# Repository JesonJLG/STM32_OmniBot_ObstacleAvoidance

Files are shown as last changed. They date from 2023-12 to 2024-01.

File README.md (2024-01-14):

## 课设题目

基于stm32的麦轮避障小车设计

## 主要任务

利用stm32f103最小系统板+相关硬件模块的方式搭建硬件平台，基于stm32库函数进行c语言编程，最终实现避障小车的实地运行。

## 详细功能描述

### 核心功能：

1. 手机app蓝牙遥控功能实现

2. 基于麦克纳姆轮的全向运动系统设计与实现

3. 在小车麦轮遥控功能的基础上迭代，增加**摇头避障、手机重力感应遥控**功能

### 其他功能：

1. 蜂鸣反馈功能
2. 速度检测与显示（测速）
3. 温度检测与显示（测温）

### 项目成果：

手机APP遥控界面展示：

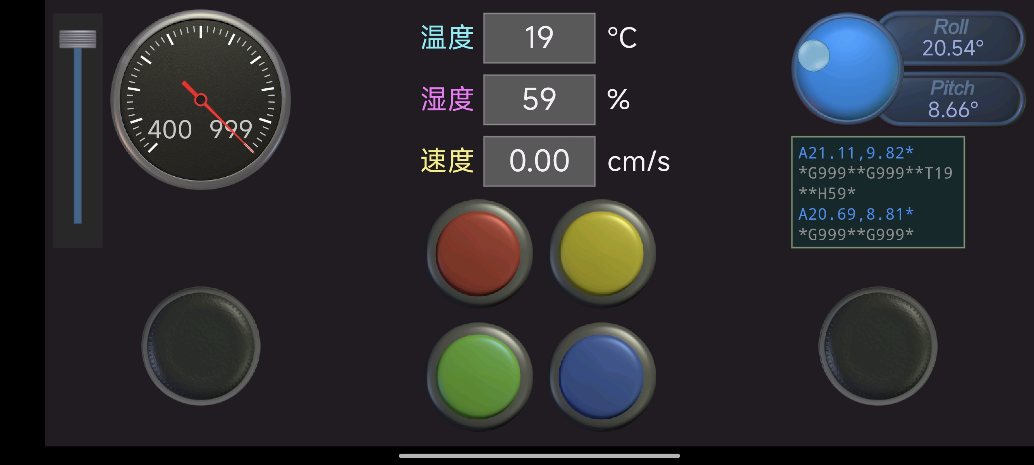
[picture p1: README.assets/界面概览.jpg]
界面概览


实物展示：

（后期测试中因误操作不慎将stm32f103c8t6最小系统板烧了，这里换用正点原子的stm32f103zet6精英板作为候补，各模块引脚均采用宏定义，故简单改动宏定义引脚即可成功移植到精英板，接线会比较麻烦）

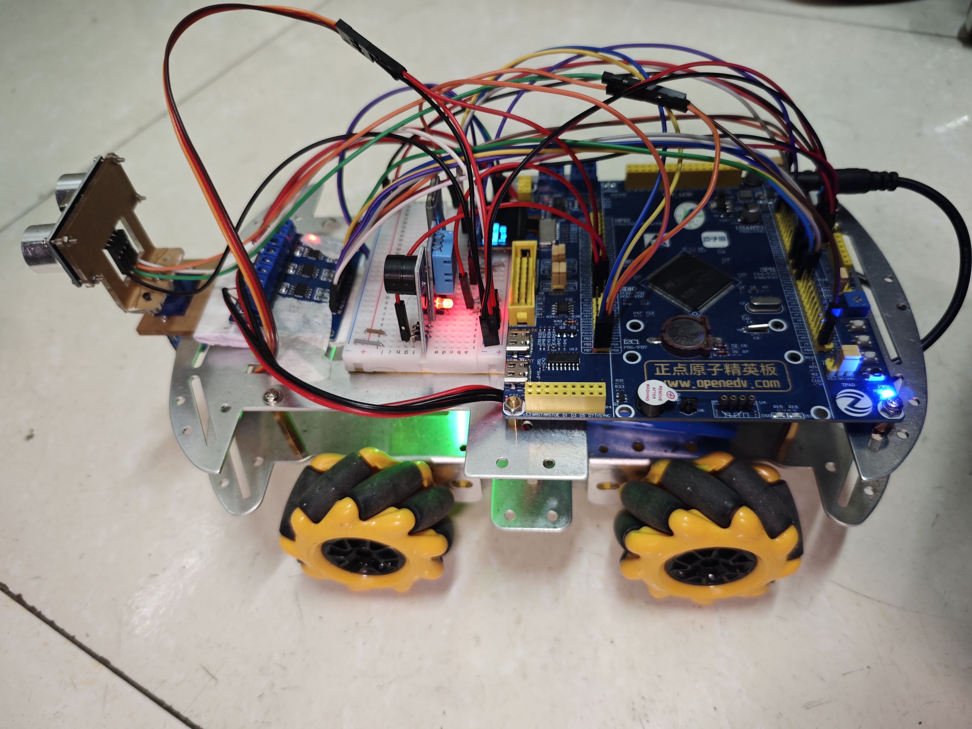
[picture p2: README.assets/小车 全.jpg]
小车 全


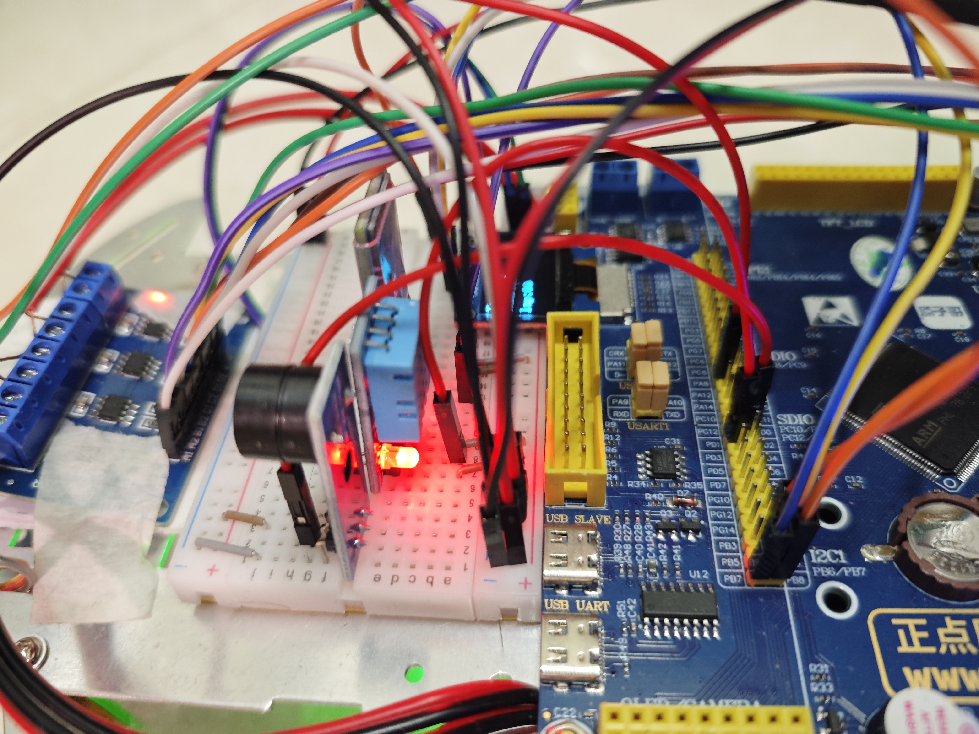
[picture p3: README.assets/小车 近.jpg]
小车 近


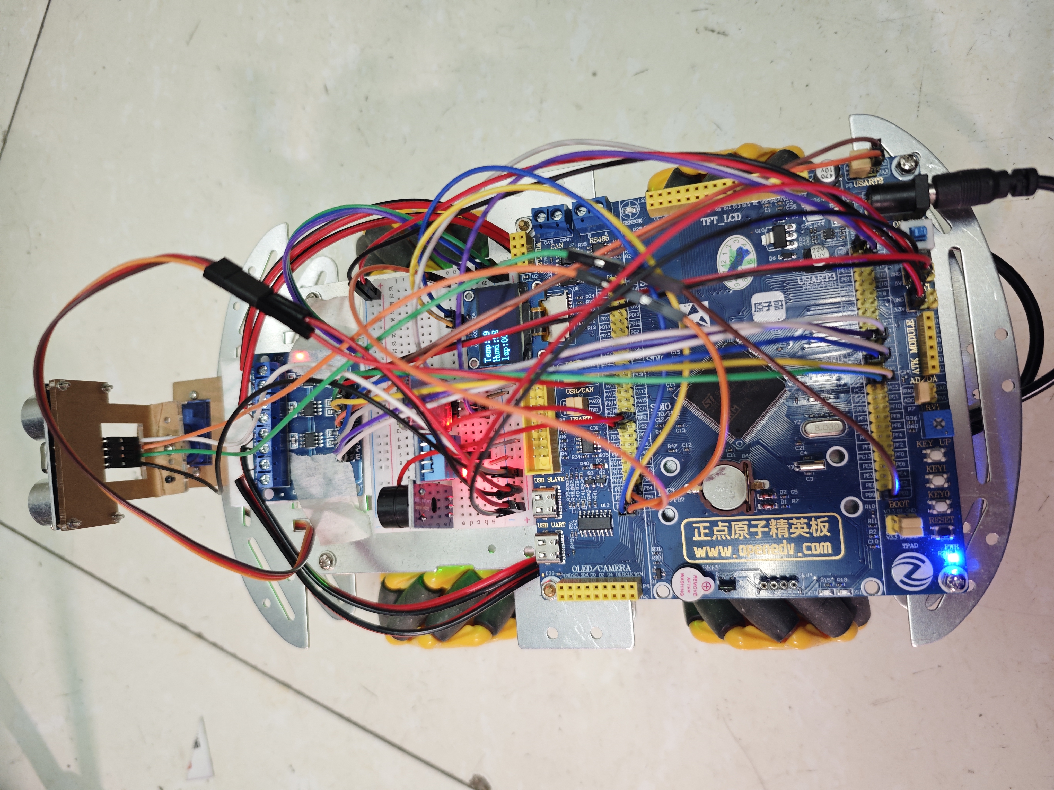
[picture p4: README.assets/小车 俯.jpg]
小车 俯


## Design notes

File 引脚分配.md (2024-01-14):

### 引脚分配

**printf串口**	USART1	PA9(TX)、PA10(RX)

**蓝牙串口**

```c
#define USART_PORT	GPIOB
#define USART_TX	GPIO_Pin_10	//PB10
#define USART_RX	GPIO_Pin_11	//PB11
#define USARTX		USART3
```

**LED指示灯**

```c
#define LED0_PORT	GPIOC
#define LED0_PIN	GPIO_Pin_13
```

```c
/*正点原子精英板*/
#define LED0_PORT	GPIOB		//DS0
#define LED0_PIN	GPIO_Pin_5	
#define LED1_PORT	GPIOE		//DS1
#define LED1_PIN	GPIO_Pin_5	
```

**四个电机**

```c
/*------------添加引脚宏定义-------------*/
/*
左后MotorA(A1,A2): PB1,PB0	TIM3_43
左前MotorB(B1,B2): PA7,PA6	TIM3_21
右前MotorC(C1,C2): PA3,PA2	TIM2_43
右后MotorD(D1,D2): PA1,PA0	TIM2_21
*/
#define MOTOR_PORT_A		GPIOB
#define MOTOR_PORT_BCD		GPIOA

#define MOTOR_TIM_AB		TIM3
#define MOTOR_TIM_CD		TIM2
///左后电机
#define MOTORA_A1		GPIO_Pin_1		//PB1
#define MOTORA_A2		GPIO_Pin_0		//PB0
///左前电机
#define MOTORB_B1		GPIO_Pin_7		//PA7
#define MOTORB_B2		GPIO_Pin_6		//PA6
///右前电机
#define MOTORC_C1		GPIO_Pin_3		//PA3
#define MOTORC_C2		GPIO_Pin_2		//PA2
///右后电机
#define MOTORD_D1		GPIO_Pin_1		//PA1
#define MOTORD_D2		GPIO_Pin_0		//PA0
```

**超声波传感器**

```c
//超声波硬件接口定义
#define HCSR04_PORT     GPIOB
#define HCSR04_CLK      RCC_APB2Periph_GPIOB
#define HCSR04_TRIG     GPIO_Pin_8
#define HCSR04_ECHO     GPIO_Pin_9
```

**舵机**

```c
#define SERVO_PORT	GPIOA
#define SERVO_PWM	GPIO_Pin_8
#define SERVO_TIM	TIM1
```

**OLED**

```c
#define OLED_PORT	GPIOB
#define OLED_SCL	GPIO_Pin_6
#define OLED_SDA	GPIO_Pin_7
```

**蜂鸣器**

```c
#define BEEP_PORT	GPIOC
#define BEEP_DIO	GPIO_Pin_14
```

```c
/*正点原子精英板*/
#define BEEP_PORT	GPIOD
#define BEEP_DIO	GPIO_Pin_0
```

**温度传感器**

```c
#define DHT11_PORT	GPIOC
#define DHT11_DATA	GPIO_Pin_15
```

```c
/*正点原子精英板*/
#define DHT11_PORT	GPIOD
#define DHT11_DATA	GPIO_Pin_1
```

**对射红外传感器**

```c
#define CNTSSR_PORT	GPIOB
#define CNTSSR_DO	GPIO_Pin_4
#define CNTSSR_EXTI	EXTI_Line4
```

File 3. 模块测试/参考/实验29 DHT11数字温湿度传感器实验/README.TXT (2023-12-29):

实验器材:
	正点原子精英STM32F103开发板
实验目的:
	学习DHT11数字温湿度传感器的使用.
	
硬件资源:
	1,DS0(连接在PB5)
	2,串口1(波特率:115200,PA9/PA10连接在板载USB转串口芯片CH340上面)
	3,ALIENTEK 2.8/3.5/4.3/7寸TFTLCD模块(通过FSMC驱动,FSMC_NE4接LCD片选/A10接RS) 
	4,DHT11传感器一个(接在PG11上). 
	
实验现象:
	本实验开机的时候先检测是否有DHT11存在，如果没有，则提示错误。只有在检测到DHT11之后才开始读取温湿
	度值，并显示在LCD上，如果发现了DHT11，则程序每隔100ms左右读取一次数据，并把温湿度显示在LCD上。同
	样我们也是用DS0来指示程序正在运行。
	 
注意事项:
	1,4.3寸和7寸屏需要比较大电流,USB供电可能不足,请用外部电源适配器(推荐外接12V 1A电源).
	2,本例程在LCD_Init函数里面(在ILI93xx.c),用到了printf,如果不初始化串口1,将导致液晶无法显示!!
	3,需自备DHT11数字温湿度传感器一个，并插在开发板的U4位置（根据丝印插，网面朝外） 

-------------------------------------------------------------------------------------------
◆其他重要连接：
  开发板光盘资料下载地址（视频+文档+源码等）：http://www.openedv.com/posts/list/13912.htm
  添加微信公众平台方法：http://www.openedv.com/posts/list/45157.htm

◆友情提示：如果您想以后及时免费的收到正点原子所有开发板资料更新增加通知，请关注微信公众平台：

 2种添加方法：（动动手提升您的学习效率，惊喜不断哦）
（1）打开微信->添加朋友->公众号->输入“正点原子”->点击关注
（2）打开微信->添加朋友->输入“alientek_stm32"->点击关注

 具体微信添加方法，请参考帖子：http://www.openedv.com/posts/list/45157.htm

			正点原子@ALIENTEK 
			广州市星翼电子科技有限公司
			电话：020-38271790
			传真：020-36773971
			购买：http://eboard.taobao.com
			公司网站：www.alientek.com
			技术论坛：www.openedv.com

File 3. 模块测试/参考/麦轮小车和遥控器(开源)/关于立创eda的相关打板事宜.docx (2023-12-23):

《关于立创eda的相关打板事宜》（个人经验，求生欲极强）

首先，成为立创eda的注册用户之后，每个月会可以在下单助手的初始界面的右下角

免费券领取（图一）中获得两张1-4层板，和一张6层板的选择权（图二），具体选择由个人自己决定（打几层的板子就用相应的优惠券）。

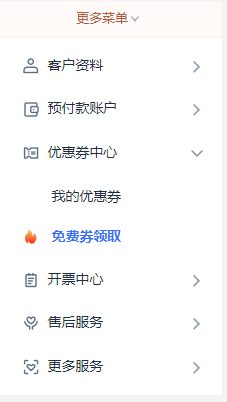
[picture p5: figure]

图一

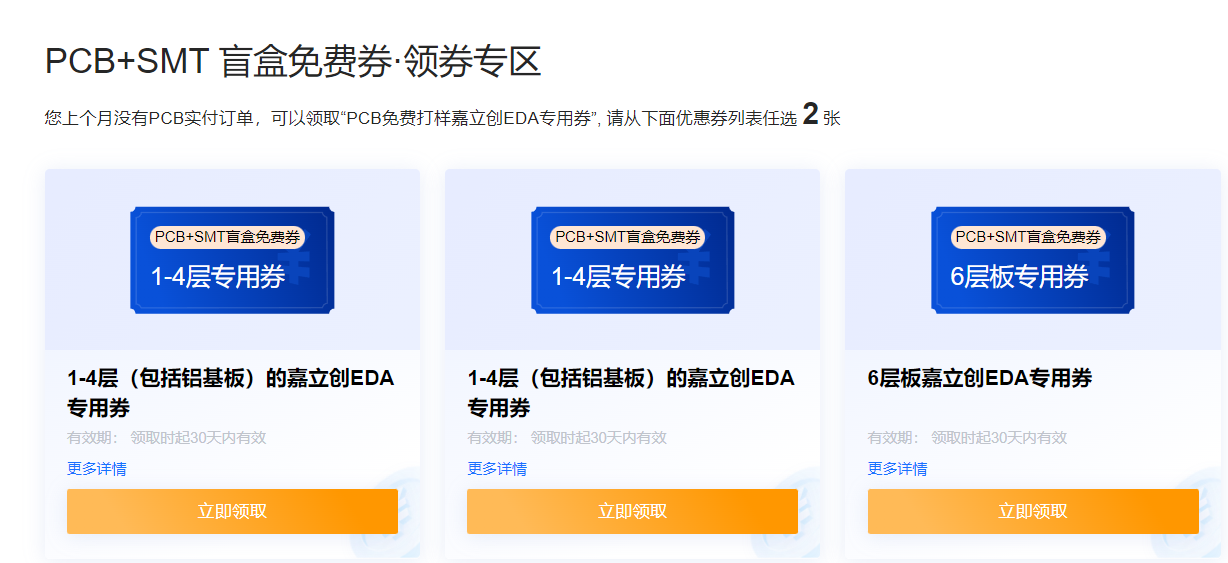
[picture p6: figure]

图二

之后就可以在pcb下单界面上传文件进行下单（注意，上传文件需要以压缩包形式上传，up主的是已经搞好的Gerber文件，所以直接上传就好，如果有自己绘制的pcb但是不是使用eda，比如使用AD的，生成的文件需要自己压缩上传，但是现在AD上传的pcb没法使用优惠券，所以建议想要节省成本的同志们使用立创eda）。

上传文件后板子的基础信息（图三）是自动出现的，层数和尺寸都是自动检测的（目前嘉立创允许的最大免费打印尺寸是10cm x 10cm），唯一需要自己决定的是板子数量，想要免费打板的话数量只能选择为5。

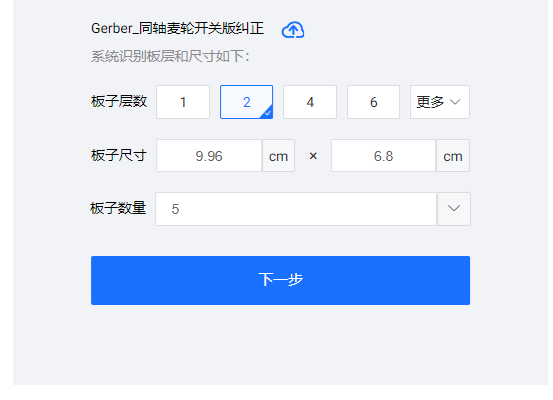
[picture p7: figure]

图三

板材类型选择FR-4即可（其他的可能不免费）。基本信息（图四）在选完板材类型后其他的保持不变即可。

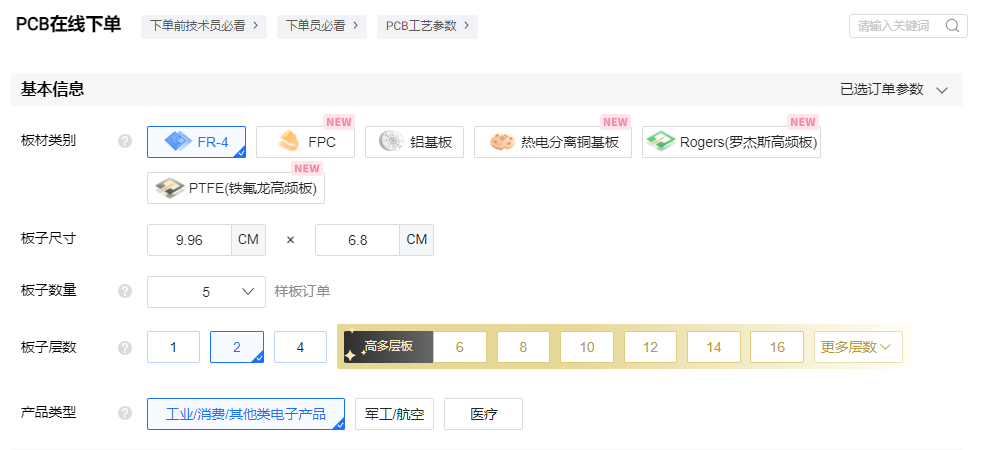
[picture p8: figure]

图四

重要事项（图五），确认生产稿就选不需要（除非想花钱）。

图五

Pcb工艺信息中拼版款数视上传文件而定，一般为1块；板子厚度为1.6；板材选项为无要求（不加价才是王道）；外层铜厚为1盎司；阻焊颜色自己选择即可（本人推荐黑色，又酷，焊出来之后看着也不是很脏，搭配洗板水清洁后效果更佳，但是需要注意的是除了绿色的板子一般48小时可以完工之外，其他所有的颜色都需要三天左右，如果急用的话建议默认绿色）；字符颜色系统默认不去管他；阻焊覆盖使用默认的过孔盖油即可（其他的要么不给用，要么得加钱）；焊盘焊盘喷镀就选有铅喷锡（问就是其他的要加钱）；不选沉金，沉金厚度就不用管；下面两项默认就好。总体如下图六

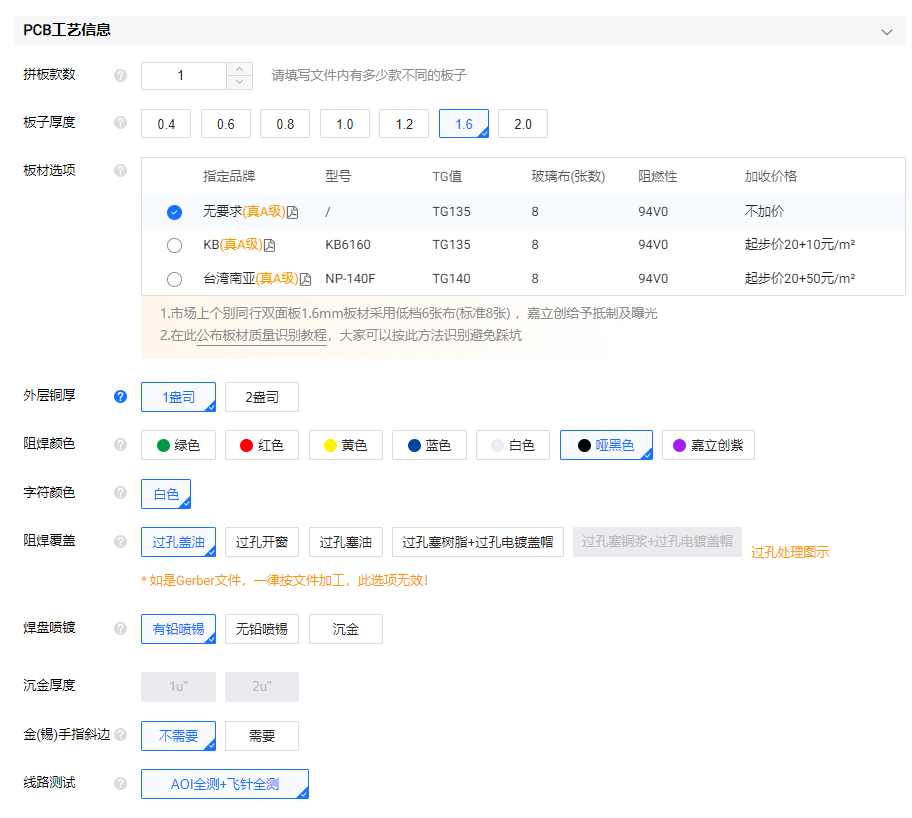
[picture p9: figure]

图六

选择交期，看个人的需求（图七）。

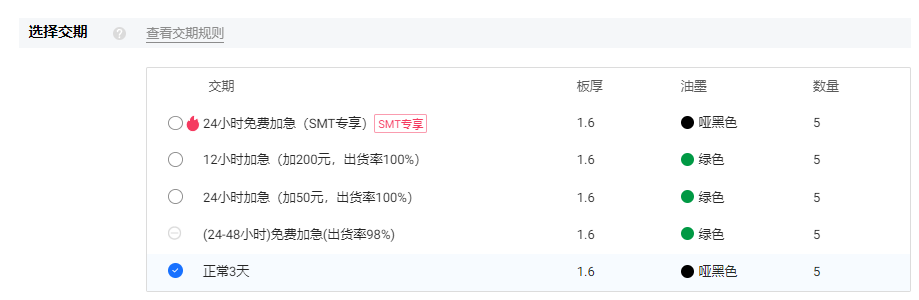
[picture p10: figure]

图七

个性化服务默认就好（图八）。

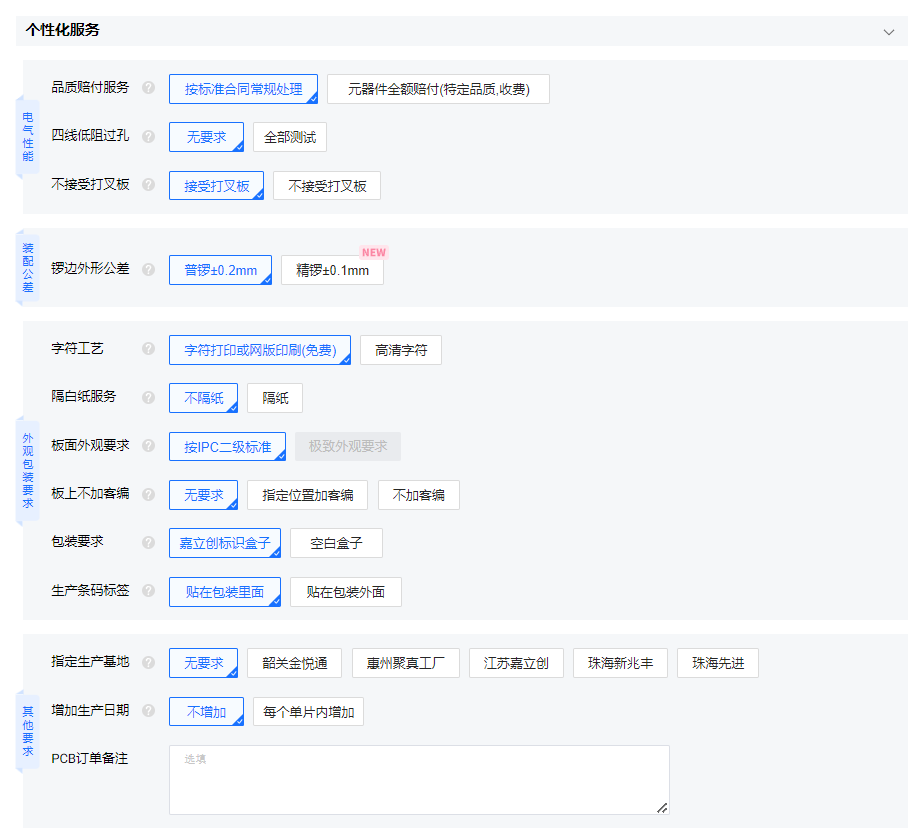
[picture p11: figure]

图八

关于SMT贴片（图九），如果对自己的焊接水平不够自信，选择此选项，eda会根据板子所需的的元器件封装在立创商城中选择对应的元器件帮你焊上（由于得加钱，本人从来没用过此选项，不知道是不是这样，不对勿喷）。

图九

关于激光钢网选项（图十），是根据pcb所用的贴片封装开相对应的钢网，目的是挤锡膏（一般使用无铅低温锡膏，一般为针管式，挤在需要放置元器件的位置上，购买加热台，将pcb放置在加热台上，待一段时间后锡膏加热为普通闪闪发亮的锡时，视情况用镊子将加热时移动的元器件调回原位。）的时候方便快捷（由于得加钱，本人从来没用过此选项，不知道是不是这样，不对勿喷）。

图十

关于完善开票信息（图十一），个人的话选择个人/普通电子发票即可，并且第一次使用时需要完善开票资料；关于地址和联系方式，各位同志想必都非常清楚。

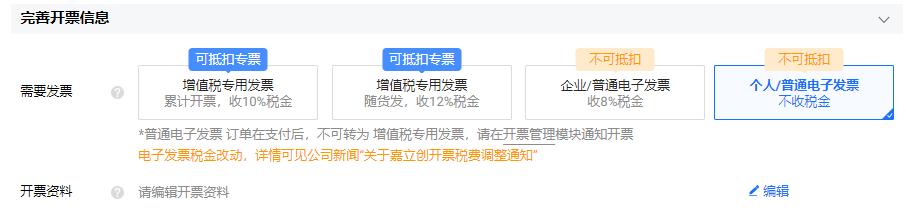
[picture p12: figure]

图十一

发货信息（图十二），收据/送货单使用电子收据单（省钱）；发货方式视情况自己决定。

图十二

选择快递（图十三），视个人情况而定。

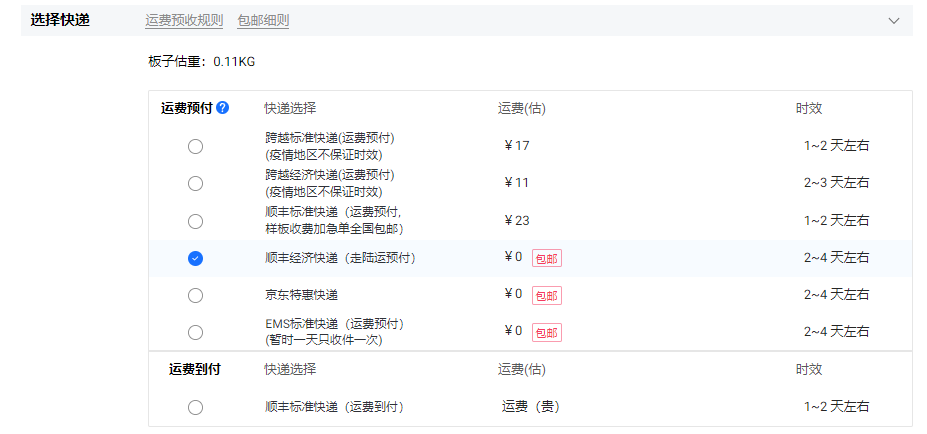
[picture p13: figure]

图十三

其他信息（图十四），个人建议手动确认，如果没有使用优惠券，不能白嫖岂不是肠子都悔青了？

图十四

最后就可以提交订单了，订单提交后，如果是手动付款的话，客服会对文件进行审核，审核通过后在图十五所示选项中查看订单信息，进行相应的付款手续（按照我上面的操作一般都是免费的）。最终效果图如图十六（本人以前打的pcb板，属于已经接收的完成状态，具体状态视情况为正在生产等）所示。

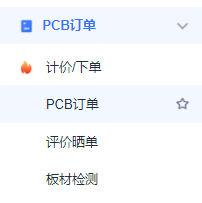
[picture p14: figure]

图十五

图十六

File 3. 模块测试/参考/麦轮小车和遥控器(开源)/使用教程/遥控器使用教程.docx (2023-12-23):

1、 左边摇杆往左或往右拨进行模式切换
2、 右边摇杆右拨进入当前模式
3、 右边摇杆左拨退出当前模式(除遥控模式外)
4、 遥控器前倾大于50度，退出遥控模式，因为遥控模式需要摇杆控 制小车运动，所以通过体感退出当前模式
5、 贪吃蛇模式蛇的运动方向由左摇杆控制
6、 遥控器的蓝牙只用于开发程序时起调试作用

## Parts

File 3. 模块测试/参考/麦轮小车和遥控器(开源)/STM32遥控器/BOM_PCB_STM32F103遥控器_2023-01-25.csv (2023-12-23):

ID | Name | Designator | Footprint | Quantity | Manufacturer Part | Manufacturer | Supplier | Supplier Part | Price
1 | 104 | C9,C6 | C0805 | 2
2 | 10k | R3,R6,JR1,JR2,R1,R2 | R0805 | 6
3 | OLED | H1 | OLED | 1
4 | 10uF | AC1 | C0805 | 1
5 | 22uF | AC2 | C0805 | 1
6 | 105 | C1,C2,C3,C4,C5 | C0805 | 5
7 | 22P | C7,C8 | C0805 | 2
8 | 100nF | JC1,JC2,JC3,JC4,JC5,JC6 | C0805 | 6
9 | AMS1117-3.3 | AU1 | SOT-223-3_L6.5-W3.4-P2.30-LS7.0-BR | 1 | AMS1117-3.3 | PUOLOP | LCSC | C351784 | 0.4095
10 | JDY-23蓝牙模块 | H2 | JDY-23蓝牙模块 | 1
11 | MPU6050模块 | H3 | MPU6050模块 | 1
12 | NRF24L01无线模块 | H4 | NRF24L01无线模块 | 1
13 | 2.54-1*4P反弯排针 | H9 | HDR-TH_4P-P2.54-H-M-W10.4 | 1 | 2.54-1*4P反弯排针 | BOOMELE(博穆精密) | LCSC | C91552 | 0.1356
14 | 510R | R4,R5 | R0805 | 2
15 | 1M | R9 | R0805 | 1
16 | JoyStick | JU1,JU2 | JOYSTICK | 2
17 | K2-3.6×6.1_SMD | KEY1 | KEY-SMD_2P-L6.2-W3.6-LS8.0 | 1 | K2-1107ST-A4SW-06 |  | LCSC | C118141 | 0.4331
18 | LED-0805_R | LED1 | LED0805_RED | 1 | 17-21SURC/S530-A3/TR8 | EVERLIGHT(台湾亿光) |  | C72037 | 0.1145
19 | LED-0805_G | LED2 | LED0805_GREEN | 1 | NCD0805G1 | 国星光电 |  | C84260 | 0.1261
20 | CONN-TH_2P-P5.00 | P2 | CONN-TH_2P-P5.00 | 1 |  |  | LCSC
21 | SS-12D06L5 | SW3 | SS-12D06 | 1 | SS-12D06L5 | XKB Enterprise | LCSC | C319015 | 2.1989
22 | STM32F103C8T6 | U1 | STM32F103C8T6LQFP-48_L7.0-W7.0-P0.50-LS9.0-BL | 1 |  |  | LCSC
23 | 8M | X1 | HC-49US_L11.5-W4.5-P4.88 | 1 | XIHCELNANF-8MHZ | TAITIEN Elec | LCSC | C295088 | 0.7692

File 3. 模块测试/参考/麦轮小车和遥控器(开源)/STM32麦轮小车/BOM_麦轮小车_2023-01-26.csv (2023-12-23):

ID | Name | Designator | Footprint | Quantity | Manufacturer Part | Manufacturer | Supplier | Supplier Part | Price
1 | 10uF | AC1 | C0805 | 1
2 | 22uF | AC2 | C0805 | 1
3 | AMS1117 | AU1 | AMS1117-3.3 | 1
4 | 105 | C1,C2,C3,C4,C5 | C0805 | 5
5 | 104 | C6 | C0805 | 1
6 | 22P | C7,C8 | C0805 | 2
7 | 100nF | C9,C10,C11,C12,C13,C14 | C0805 | 6
8 | HX25035-2A | CN1,CN2,CN3,CN4 | CONN-TH_P2.50_HX25035-2A | 4 | HX25035-2A | HX(红星) | LCSC | C442378 | 0.0935
9 | HDR-F-2.54_1x8 | H1,H3,H5,H6 | HDR-F-2.54_1X8 | 4 |  |  | LCSC | C225505 | 1.1165
10 | JDY-23蓝牙模块 | H2 | JDY-23蓝牙模块 | 1
11 | NRF24L01无线模块 | H4 | NRF24L01无线模块 | 1
12 | HDR-F-2.54_1x4 | H15 | HDR-F-2.54_1X4 | 1 |  |  | LCSC | C225501 | 0.4928
13 | STlink | H16 | STLINK | 1
14 | K2-3.6×6.1_SMD | KEY1 | KEY-SMD_2P-L6.2-W3.6-LS8.0 | 1 | K2-1107ST-A4SW-06 |  | LCSC | C118141 | 0.4331
15 | LED-0805_R | LED9 | LED0805_RED | 1 | 17-21SURC/S530-A3/TR8 | EVERLIGHT(台湾亿光) |  | C72037 | 0.1145
16 | LED-0805_G | LED10 | LED0805_GREEN | 1 | NCD0805G1 | 国星光电 |  | C84260 | 0.1261
17 | WS2812B-V5/W | LED11,LED12,LED13,LED14,LED15,LED16 | LED-SMD_L5.0-W5.0-P3.20-LS5.4-TL | 6 | WS2812B-V5/W | worldsemi | LCSC | C2874885 | 0.6626
18 | CONN-TH_2P-P5.00 | P2 | CONN-TH_2P-P5.00 | 1 |  |  | LCSC
19 | 10k | R1,R2 | R0805 | 2
20 | 510R | R4,R5 | R0805 | 2
21 | 1M | R9 | R0805 | 1
22 | SS-12D06L5 | SW3 | SS-12D06 | 1 | SS-12D06L5 | XKB Enterprise | LCSC | C319015 | 2.1989
23 | STM32F103C8T6 | U1 | STM32F103C8T6LQFP-48_L7.0-W7.0-P0.50-LS9.0-BL | 1 |  |  | LCSC
24 | Mini降压模块 | U2 | MINI降压模块 | 1
25 | 8M | X1 | HC-49US_L11.5-W4.5-P4.88 | 1 | XIHCELNANF-8MHZ | TAITIEN Elec | LCSC | C295088 | 0.7692

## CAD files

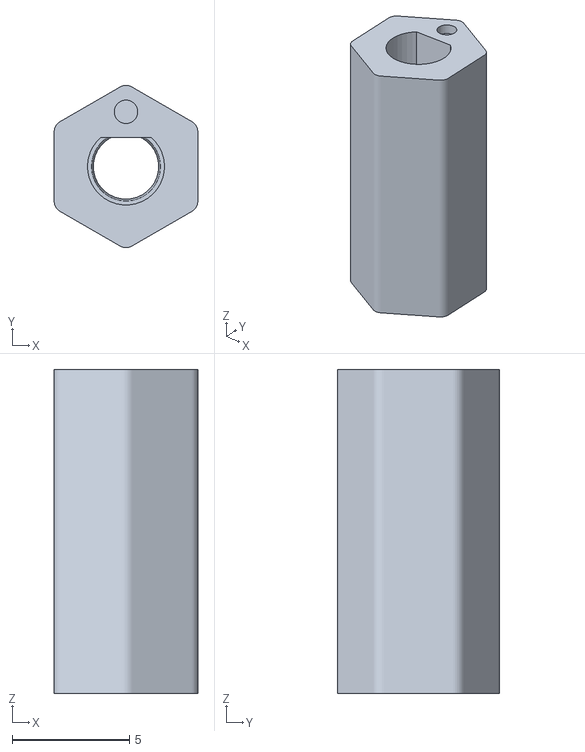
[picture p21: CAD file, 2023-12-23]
3. 模块测试/参考/麦轮小车和遥控器(开源)/3D打印模型/N20电机配件3D文件/48mm麦轮联轴器(打印误差难控制).STL
6.12 x 6.91 x 13.8

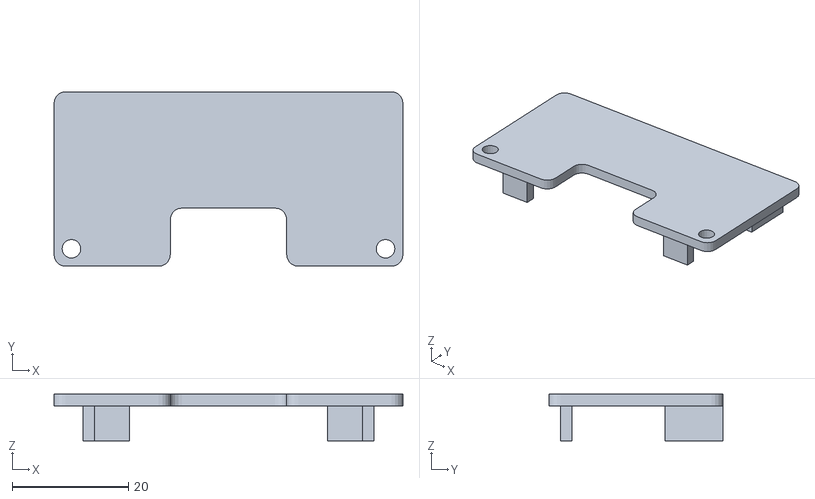
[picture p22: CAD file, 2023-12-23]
3. 模块测试/参考/麦轮小车和遥控器(开源)/3D打印模型/麦轮小车电池支架.stl
60.0 x 30.0 x 8.00

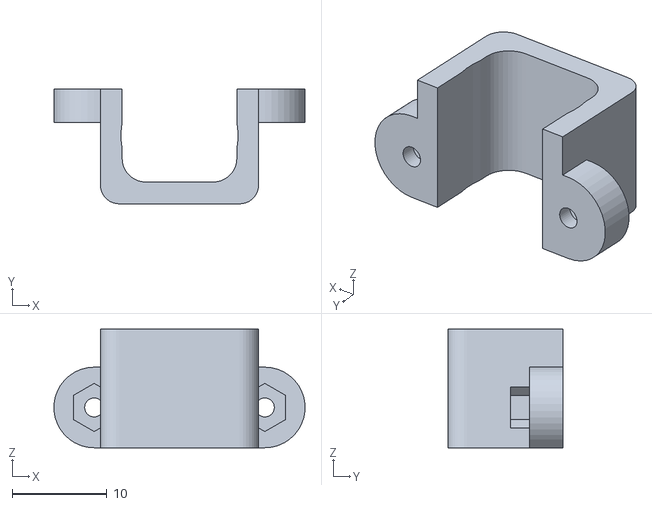
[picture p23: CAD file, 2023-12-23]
3. 模块测试/参考/麦轮小车和遥控器(开源)/3D打印模型/N20电机配件3D文件/N20电机固定座.STL
26.5 x 12.1 x 12.5

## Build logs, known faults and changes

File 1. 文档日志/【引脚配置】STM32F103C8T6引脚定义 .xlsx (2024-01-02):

STM32F103C8T6引脚定义表
引脚号 | 引脚名称 | 类型 | I/O口电平 | 主功能 | 默认复用功能 | 重定义功能
1 | VBAT | S |  | VBAT
2 | PC13-TAMPER-RTC | I/O |  | PC13 | TAMPER-RTC |  | 特殊功能待定 |  | LED
3 | PC14-OSC32_IN | I/O |  | PC14 | OSC32_IN |  |  |  | BEEP
4 | PC15-OSC32_OUT | I/O |  | PC15 | OSC32_OUT |  |  |  | DHT11
5 | OSC_IN | I |  | OSC_IN
6 | OSC_OUT | O |  | OSC_OUT
7 | NRST | I/O |  | NRST
8 | VSSA | S |  | VSSA
9 | VDDA | S |  | VDDA
10 | PA0-WKUP | I/O |  | PA0 | WKUP/USART2_CTS/ADC12_IN0/TIM2_CH1_ETR |  | USART2/ADC12_0123/TIM2_1234 |  | 右后电机D
11 | PA1 | I/O |  | PA1 | USART2_RTS/ADC12_IN1/TIM2_CH2
12 | PA2 | I/O |  | PA2 | USART2_TX/ADC12_IN2/TIM2_CH3 |  |  |  | 右前电机C
13 | PA3 | I/O |  | PA3 | USART2_RX/ADC12_IN3/TIM2_CH4
14 | PA4 | I/O |  | PA4 | SPI1_NSS/USART2_CK/ADC12_IN4 |  | SPI1/ADC12_4567 | ADC12_IN45
15 | PA5 | I/O |  | PA5 | SPI1_SCK/ADC12_IN5
16 | PA6 | I/O |  | PA6 | SPI1_MISO/ADC12_IN6/TIM3_CH1 | TIM1_BKIN |  | TIM3_1234 | 左前电机B
17 | PA7 | I/O |  | PA7 | SPI1_MOSI/ADC12_IN7/TIM3_CH2 | TIM1_CH1N
18 | PB0 | I/O |  | PB0 | ADC12_IN8/TIM3_CH3 | TIM1_CH2N | ADC12_89/TIM3_34 |  | 左后电机A
19 | PB1 | I/O |  | PB1 | ADC12_IN9/TIM3_CH4 | TIM1_CH3N
20 | PB2 | I/O | FT | PB2/BOOT1
21 | PB10 | I/O | FT | PB10 | I2C2_SCL/USART3_TX | TIM2_CH3 | I2C2/USART3 |  | 蓝牙串口3
22 | PB11 | I/O | FT | PB11 | I2C2_SDA/USART3_RX | TIM2_CH4
23 | VSS_1 | S |  | VSS_1
24 | VDD_1 | S |  | VDD_1
25 | PB12 | I/O | FT | PB12 | SPI2_NSS/I2C2_SMBAI/USART3_CK/TIM1_BKIN |  | SPI2（36MHz）
26 | PB13 | I/O | FT | PB13 | SPI2_SCK/USART3_CTS/TIM1_CH1N
27 | PB14 | I/O | FT | PB14 | SPI2_MISO/USART3_RTS/TIM1_CH2N
28 | PB15 | I/O | FT | PB15 | SPI2_MOSI/TIM1_CH3N
29 | PA8 | I/O | FT | PA8 | USART1_CK/TIM1_CH1/MCO |  | USART1/TIM1_1234E | MCO | 舵机PWM输出 | 兼具1s定时中断功能
30 | PA9 | I/O | FT | PA9 | USART1_TX/TIM1_CH2 |  |  |  | printf调试串口
31 | PA10 | I/O | FT | PA10 | USART1_RX/TIM1_CH3
32 | PA11 | I/O | FT | PA11 | USART1_CTS/USBDM/CAN_RX/TIM1_CH4 |  |  | USB/CAN | 备用PWM输出
33 | PA12 | I/O | FT | PA12 | USART1_RTS/USBDP/CAN_TX/TIM1_ETR
34 | PA13 | I/O | FT | JTMS/SWDIO |  | PA13 | 勿动
35 | VSS_2 | S |  | VSS_2
36 | VDD_2 | S |  | VDD_2
37 | PA14 | I/O | FT | JTCK/SWCLK |  | PA14
38 | PA15 | I/O | FT | JTDI |  | TIM2_CH1_ETR/PA15/SPI1_NSS | SPI1 | TIM2_12
39 | PB3 | I/O | FT | JTDO |  | PB3/TRACESWO/TIM2_CH2/SPI1_SCK
40 | PB4 | I/O | FT | NJTRST |  | PB4/TIM3_CH1/SPI1_MISO |  | TIM3_12 | 对射红外（外部中断）
41 | PB5 | I/O |  | PB5 | I2C1_SMBAI | TIM3_CH2/SPI1_MOSI |  |  |  | 精英版DS0
42 | PB6 | I/O | FT | PB6 | I2C1_SCL/TIM4_CH1 | USART1_TX | TIM4_1234 | I2C1 | OLED | 超声波测距占用了TIM4的内部计数器，4个通道均无法再作为PWM输出
43 | PB7 | I/O | FT | PB7 | I2C1_SDA/TIM4_CH2 | USART1_RX
44 | BOOT0 | I |  | BOOT0
45 | PB8 | I/O | FT | PB8 | TIM4_CH3 | I2C1_SCL/CAN_RX |  |  | 超声波
46 | PB9 | I/O | FT | PB9 | TIM4_CH4 | I2C1_SDA/CAN_TX
47 | VSS_3 | S |  | VSS_3
48 | VDD_3 | S |  | VDD_3

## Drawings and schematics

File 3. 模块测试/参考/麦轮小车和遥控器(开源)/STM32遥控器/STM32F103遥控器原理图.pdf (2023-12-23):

## GND

## VCC3V3

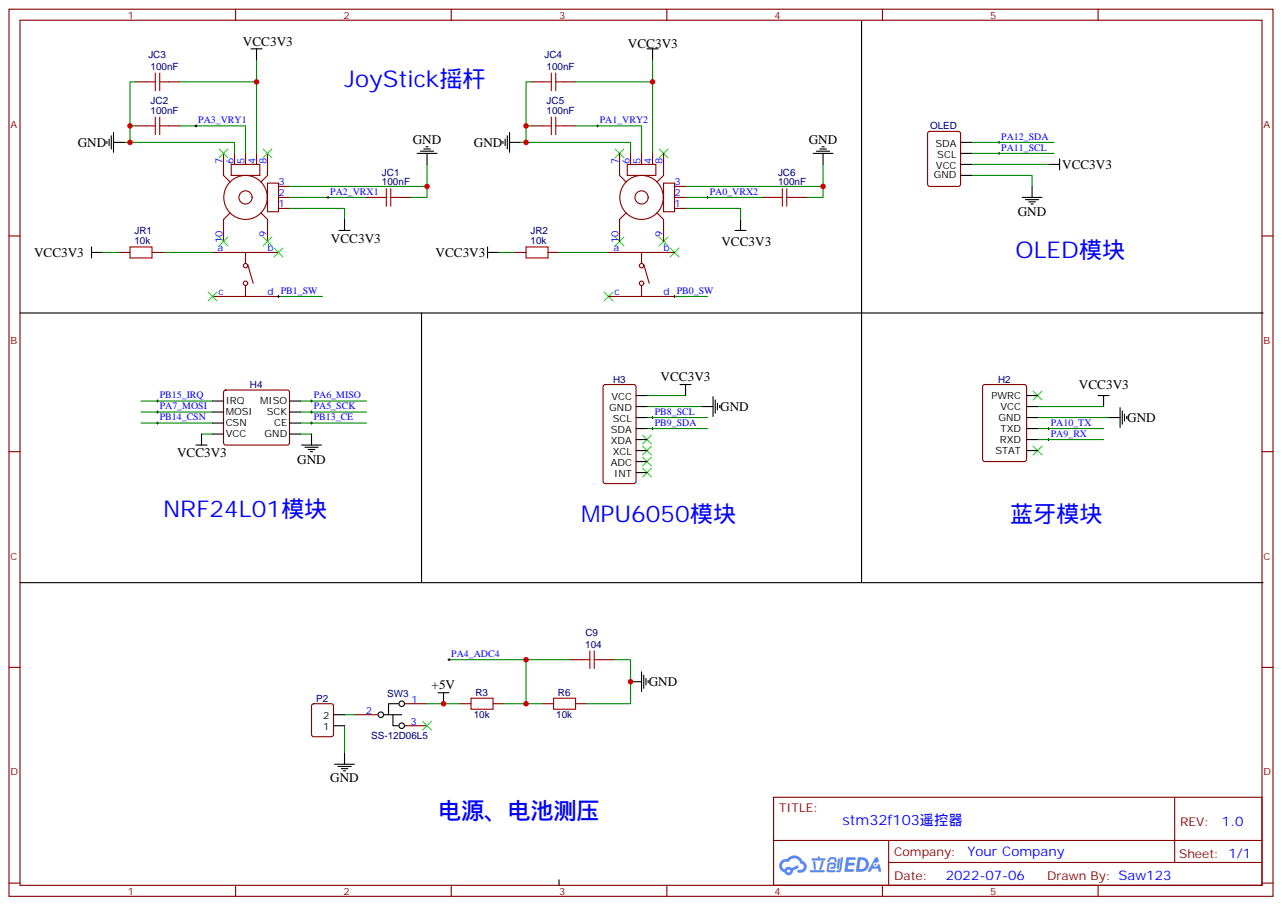
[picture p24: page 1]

GND | GND | GND | GND

## VCC3V3 VCC3V3 VCC3V3 VCC3V3

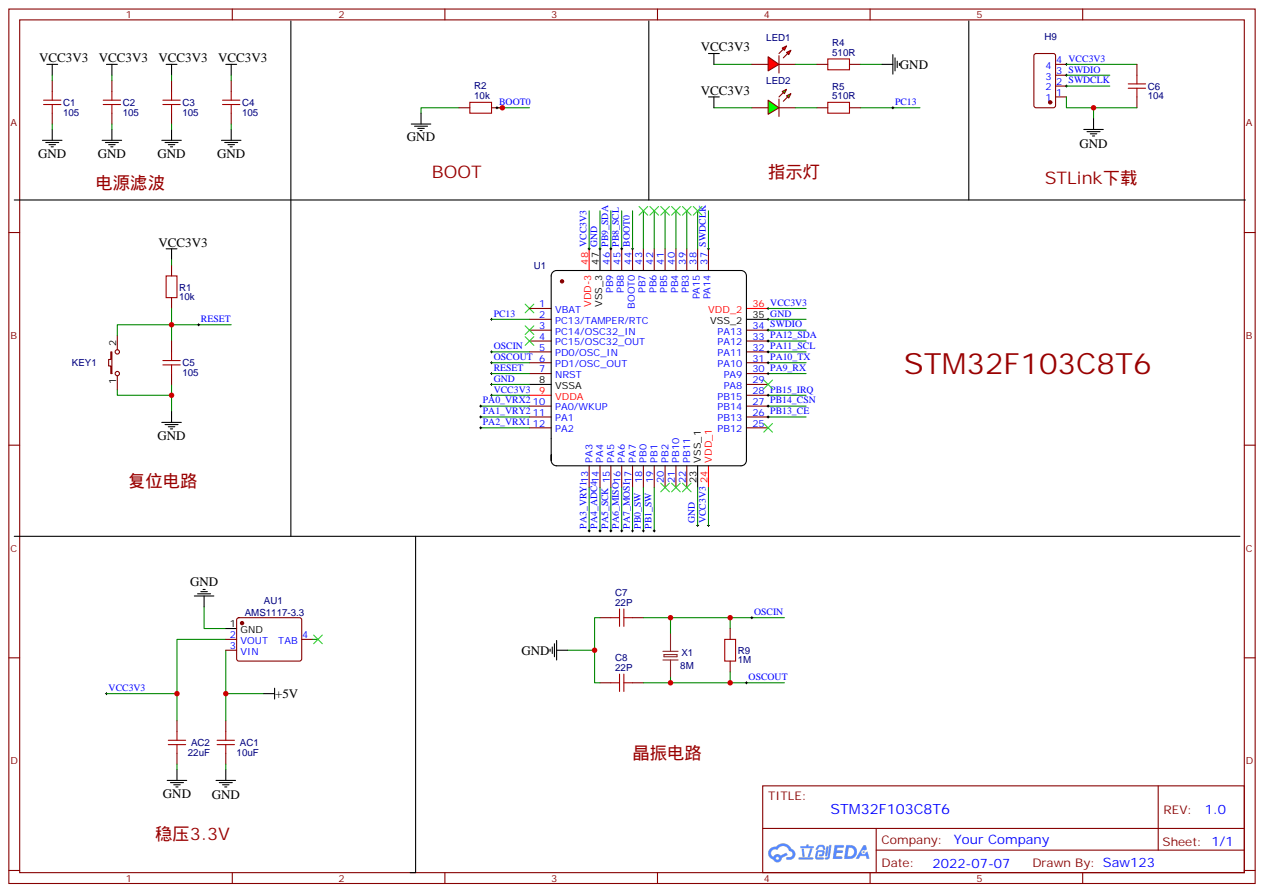
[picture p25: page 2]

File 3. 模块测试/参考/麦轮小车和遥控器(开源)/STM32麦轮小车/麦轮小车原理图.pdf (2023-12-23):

## VCC3V3 GND

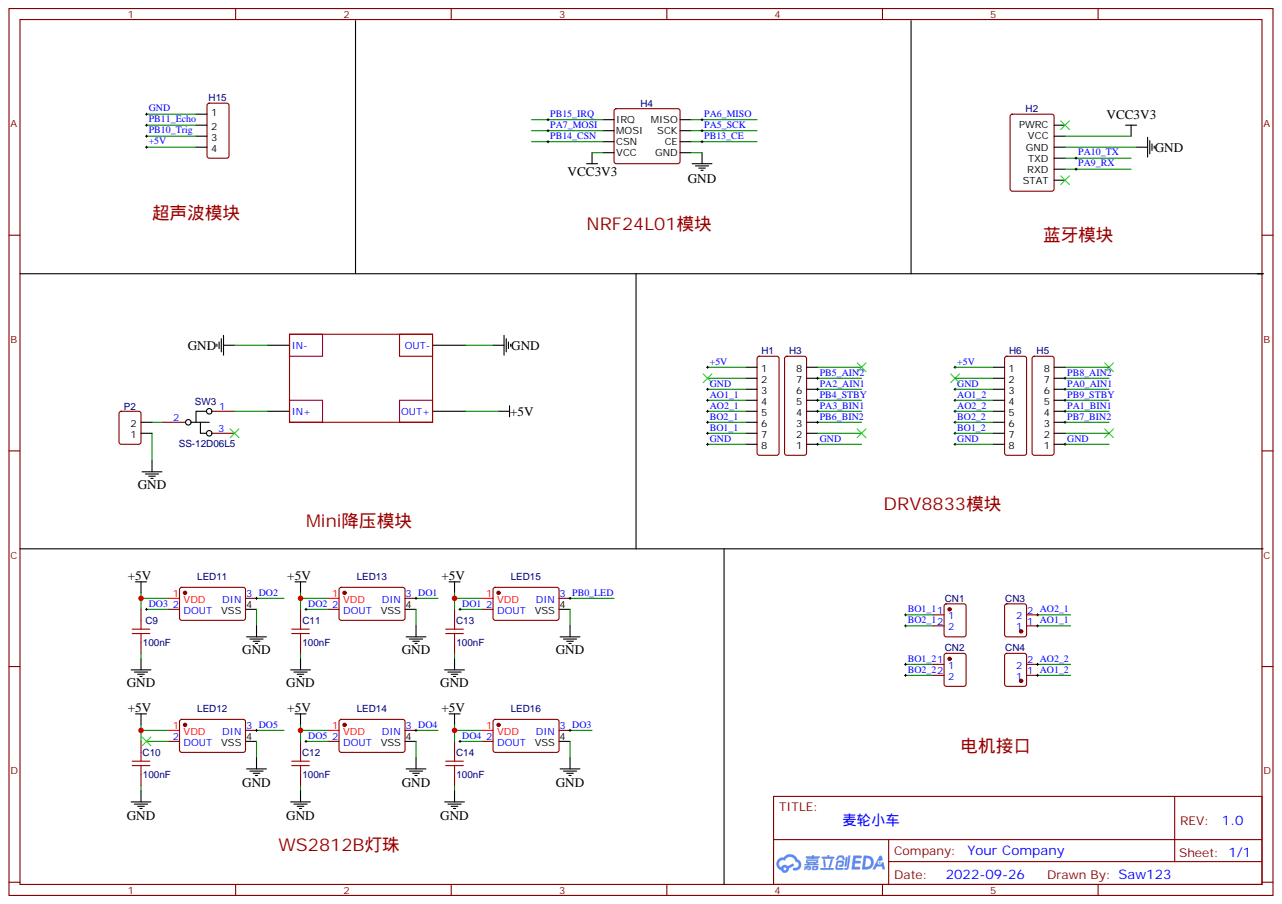
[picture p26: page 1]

电源滤波 | BOOT | 指示灯 | STLink下载 GND

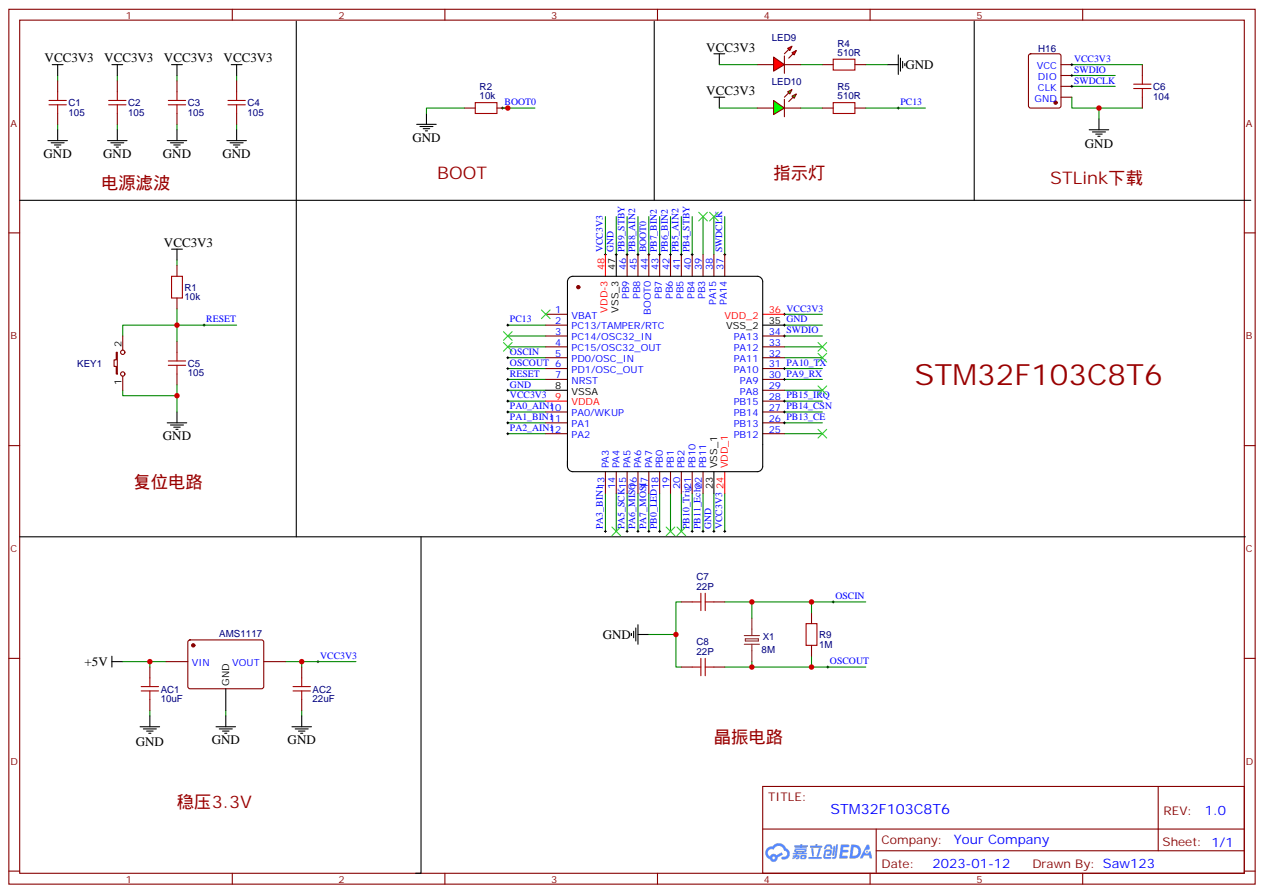
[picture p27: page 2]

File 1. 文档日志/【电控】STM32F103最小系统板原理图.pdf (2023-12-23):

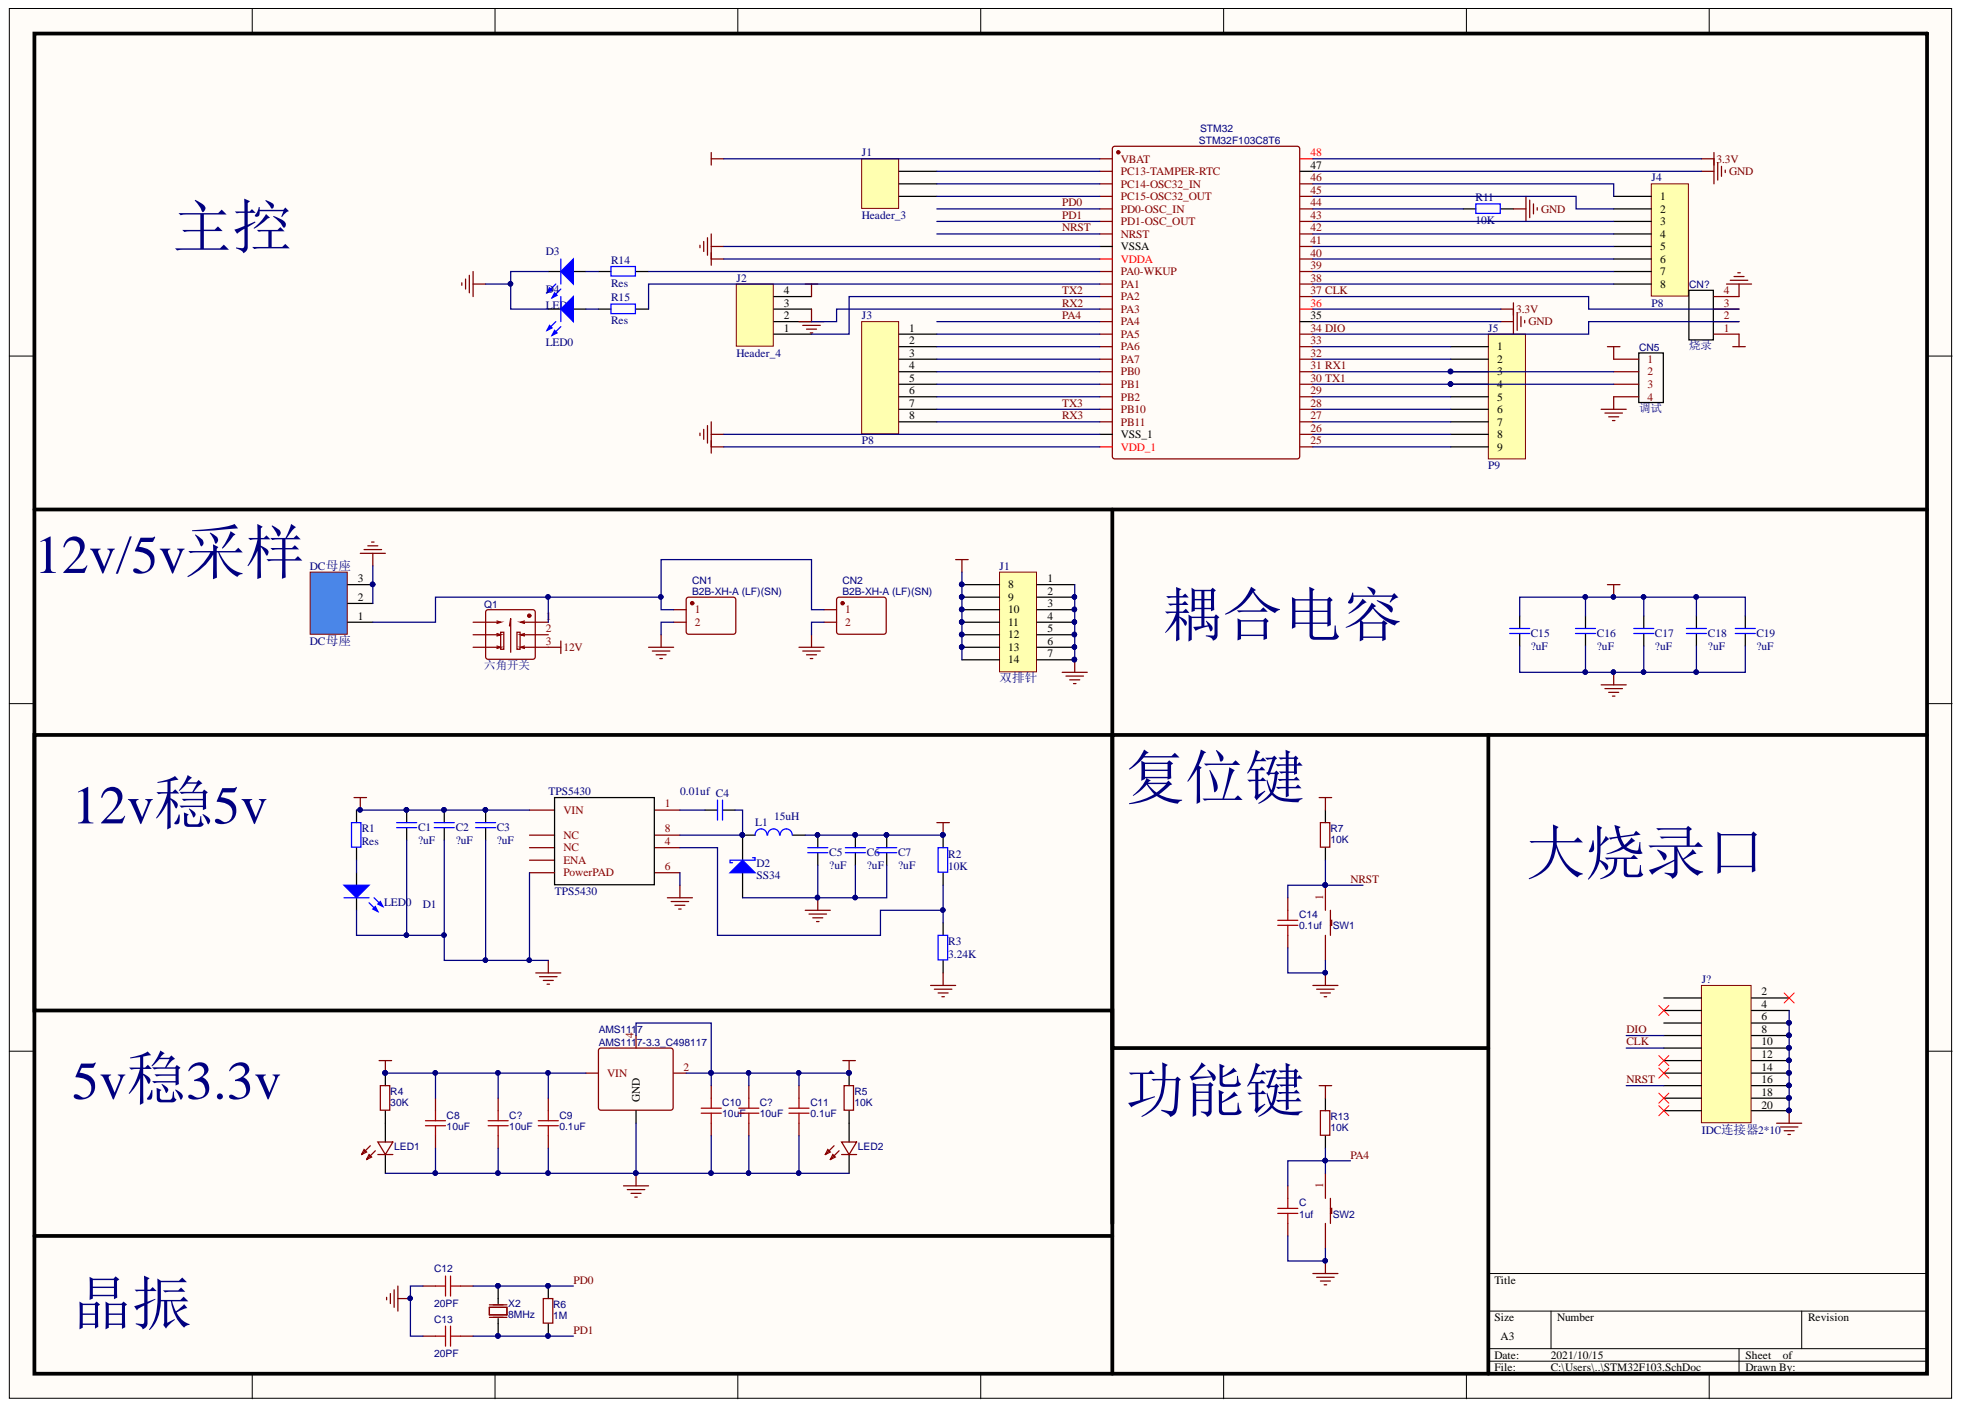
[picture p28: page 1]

4 | TX2
3 | RX2
2 | J3 PA4

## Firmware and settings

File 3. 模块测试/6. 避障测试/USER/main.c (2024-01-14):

/****************************************************************************

麦轮小车引脚分配

N20电机

STBY1:PB4    STBY2:PB9

1:PA2,PB6      2:PA3,PB5
3:PA0,PB8      4:PA1,PB7

蓝牙模块	usart2
超声波模块	TRIG:PB10         ECHO:PB11

************************************************************************************/
#include "stm32f10x.h"                  // Device header
#include "sys.h"
#include "delay.h"
#include "usart.h"
#include "led.h"
#include "motor.h"
#include "control.h"
#include "hcsr.h"
#include "beep.h"

extern u8 mode_flag;	//初始为0

void motor_test(void);

int main(void)
{
	delay_init();	    	 //延时函数初始化	 
	NVIC_PriorityGroupConfig(NVIC_PriorityGroup_2);
	LED_Init();
	USART1_Init(115200);	//printf
	USART2_Init(9600);		//BT06
	Motor_Init();
	Hcsr04_Init();			//超声波
	BEEP_Init();
	BEEP_Ring();
	
	//Wait_BT_CONNECTED();

	while (1)
	{
		//printf("11111\r\n");
		//Control();
		Hcsr04_Text();
	}
}

void motor_test(void)
{
	printf("电机测试\r\n");
	Car_Forward(500);
	delay_ms(1800);
	Car_Backward(500);
	delay_ms(1800);
	Car_TransLeft(500);
	delay_ms(1800);
	Car_TransRight(500);
	delay_ms(1800);
	Car_TurnLeft(500);
	delay_ms(1800);
	Car_Stop();
	delay_ms(1800);
	Car_TurnRight(500);
	delay_ms(1800);
}

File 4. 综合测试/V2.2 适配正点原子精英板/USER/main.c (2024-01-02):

/****************************************************************************

麦轮小车引脚分配

N20电机

STBY1:PB4    STBY2:PB9

1:PA2,PB6      2:PA3,PB5
3:PA0,PB8      4:PA1,PB7

蓝牙模块	usart2
超声波模块	TRIG:PB10         ECHO:PB11

************************************************************************************/
#include "stm32f10x.h"                  // Device header
#include "sys.h"
#include "delay.h"
#include "usart.h"
#include "led.h"
#include "motor.h"
#include "control.h"
#include "hcsr.h"
#include "dht11.h"
#include "beep.h"
#include "servo.h"
#include "oled.h"
#include "countsensor.h"
#include "serial.h"

//extern unsigned int rec_data[4];
//extern u8 mode_flag;			//初始为0
//extern char Pwm_RxPacket[20];	//"P[...]\r\n"	Pwm_RxPacket[0]为pwm_limit
u8 t;
u8 temperature, humidity;
extern int cnt;				//对射红外外部中断次数
int girdCount = 20;		//码盘格子数
float lap;				//轮子圈数
float perimeter = 8.1;	//轮子周长 2.575cm * 3.14 ≈ 8.1cm
float distance;			//路程
float speed;			//速度
int time;
extern char Pwm_RxFlag;

void analyzeIRSensorData_1s(void);

int main(void)
{
	delay_init();	    	 //延时函数初始化	 
	NVIC_PriorityGroupConfig(NVIC_PriorityGroup_2);
	LED_Init();
	USART1_Init(115200);	//printf
	Serial_Init(9600);		//BT06
	Motor_Init();
	Hcsr04_Init();			//超声波
	CountSensor_Init();
	OLED_Init();
	BEEP_Init();
	BEEP_Ring();
	Servo_Init();
	Servo_SetAngle(90);
	OLED_ShowString(1, 1, "Temp:00");
	OLED_ShowString(2, 1, "Humi:00");
	OLED_ShowString(3, 1, "lap:00");
	printf("123\r\n");
	
	
	while (DHT11_Init())	//DHT11初始化
	{
		printf("DHT11 Error\r\n");
		delay_ms(200);
	}

	Wait_BT_CONNECTED(); 	//等待蓝牙连接成功
	while (1) 
	{
		Control();
		analyzeIRSensorData_1s();
		if (t % 10 == 0)			//每100ms读取一次
		{
			DHT11_Read_Data(&temperature, &humidity);	//读取温湿度值
			OLED_ShowNum(1, 6, temperature, 2);
			OLED_ShowNum(2, 6, humidity, 2);
			Serial_Printf("*T%d*", temperature);
			Serial_Printf("*H%d*", humidity);
		}
		delay_ms(10);
		t++;
		if (t == 20)
		{
			t = 0;
			LED0 = !LED0;	//LED不断闪烁
		}
		
	}
}

void analyzeIRSensorData_1s(void) 
{
	if(time == 50)//20ms*50 = 1000ms = 1s
	{
		time = 0;
		lap = cnt / (float)girdCount;	//多少圈
		speed = lap * perimeter;		//速度cm/s
		cnt = 0;						//中断次数
		OLED_ShowNum(3, 6, lap, 2);
		Serial_Printf("*D%.2f*", speed);
	}
}

////TIM1更新中断函数	20ms一次
void TIM1_UP_IRQHandler(void)
{
	if (TIM_GetITStatus(TIM1, TIM_IT_Update) == SET)
	{
		time ++;
//		analyzeIRSensorData_1s();
		TIM_ClearITPendingBit(TIM1, TIM_IT_Update);
	}
}

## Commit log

2023-12-23 first commit 模块测试
    [48mm麦轮联轴器(打印误差难控制).STL, BOM_PCB_STM32F103遥控器_2023-01-25.csv, BOM_麦轮小车_2023-01-26.csv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]
2023-12-23 添加并完善 蓝牙遥控数据解析模块 实现手机APP蓝牙遥控小车进行全向运动
2023-12-24 添加各种模块测试 未完成
    [【引脚配置】STM32F103C8T6引脚定义 .xlsx]
2023-12-25 优化麦轮算法 添加避障功能 优化蓝牙串口接收 增加蜂鸣响应功能等
2023-12-26 改善避障算法
2023-12-29 9. 测温+蜂鸣+OLED 修改bug 跑通测试
    [【引脚配置】STM32F103C8T6引脚定义 .xlsx]
2023-12-29 添加10. OLED+蜂鸣+测温+对射红外
    [【引脚配置】STM32F103C8T6引脚定义 .xlsx]
2023-12-30 模块代码集成 添加综合测试
2023-12-31 修改综合测试 优化蓝牙串口通讯协议
2023-12-31 综合测试V1
2023-12-31 更新综合测试V1.1 添加对射红外传感器测速功能
    [【引脚配置】STM32F103C8T6引脚定义 .xlsx]
2024-01-01 添加综合测试V2.1 适配正点原子精英板 跑通测试 基本完全体
    [【引脚配置】STM32F103C8T6引脚定义 .xlsx]
2024-01-02 更新综合测试V2.1 适配正点原子精英板
2024-01-02 添加综合测试V2.3 课设演示版本
    [【引脚配置】STM32F103C8T6引脚定义 .xlsx]
2024-01-08 更新综合测试V2.3 课设演示版本
2024-01-14 更新文档
2024-01-14 更新README.md
